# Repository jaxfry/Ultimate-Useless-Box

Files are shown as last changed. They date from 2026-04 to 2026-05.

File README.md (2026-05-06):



[][stars-url]
[][issues-url]
[][license-url]

<!-- PROJECT LOGO -->
<br />
<div align="center">
  <a href="https://github.com/jaxfry/Ultimate-Useless-Box">
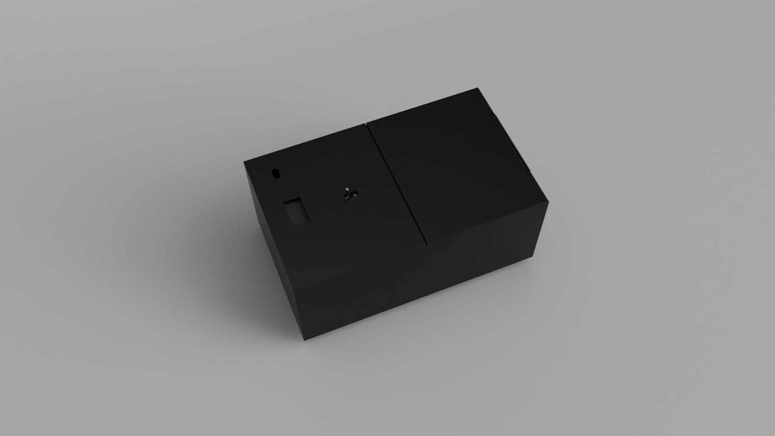
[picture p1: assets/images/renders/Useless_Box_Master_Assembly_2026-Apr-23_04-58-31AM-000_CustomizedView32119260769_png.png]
    
  </a>

<h3 align="center">Ultimate Useless Box</h3>

  <p align="center">
    The Ultimate Useless Box, a box that does nothing, with style.
    <br />
    <br />
    <a href="#gallery--renders">View Renders</a>
    &middot;
    <a href="#custom-pcb">View PCB</a>
  </p>
</div>

<!-- TABLE OF CONTENTS -->
<details>
  <summary>Table of Contents</summary>
  <ol>
    <li>
      <a href="#about-the-project">About The Project</a>
      <ul>
        <li><a href="#built-with">Built With</a></li>
      </ul>
    </li>
    <li>
      <a href="#gallery--renders">Gallery & Renders</a>
    </li>
    <li>
      <a href="#custom-pcb">Custom PCB</a>
    </li>
    <li><a href="#bill-of-materials">Bill of Materials</a></li>
    <li><a href="#license">License</a></li>
  </ol>
</details>

<!-- ABOUT THE PROJECT -->
## About The Project

While most useless boxes just flip a switch, this one has personality. Powered by an **ESP32-S3**, this box uses a Time-of-Flight sensor to detect your hand before you even push the swtich, allowing the box to react by driving away, with the OLED screen, or countless other ways!
This project is heavily inspired by LuuMa EV3.
When I saw that video many years ago, I realized I wanted my own useless box. Then I realized that Lego Mindstorm kits are prohibitively expensive. Many years later and I decided to make my own using standard electronic components with a few unique twists of my own :)

**Key Features:**
* **OLED Display** for animated faces.
* **Fun Built in Power Management:** Mainly for learning and fun but we charge over usb-C!
* **Wheels** for driving away.
* **TOF** sensor for detecting hands.
* **A Retractable Switch**
<p align="right">(<a href="#readme-top">back to top</a>)</p>

### Built With

*   
*   
*   
*   

<p align="right">(<a href="#readme-top">back to top</a>)</p>

### Custom PCB
<div align="center">
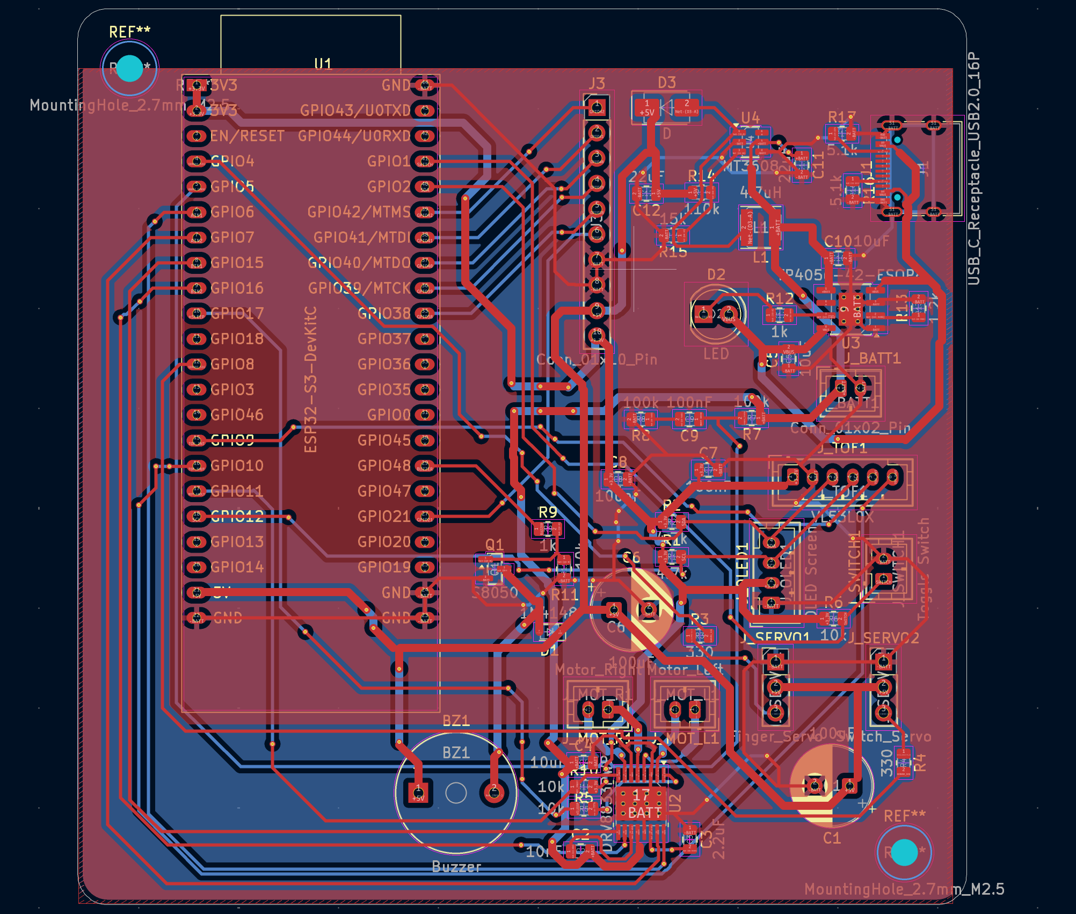
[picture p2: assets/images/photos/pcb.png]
PCB Front
  
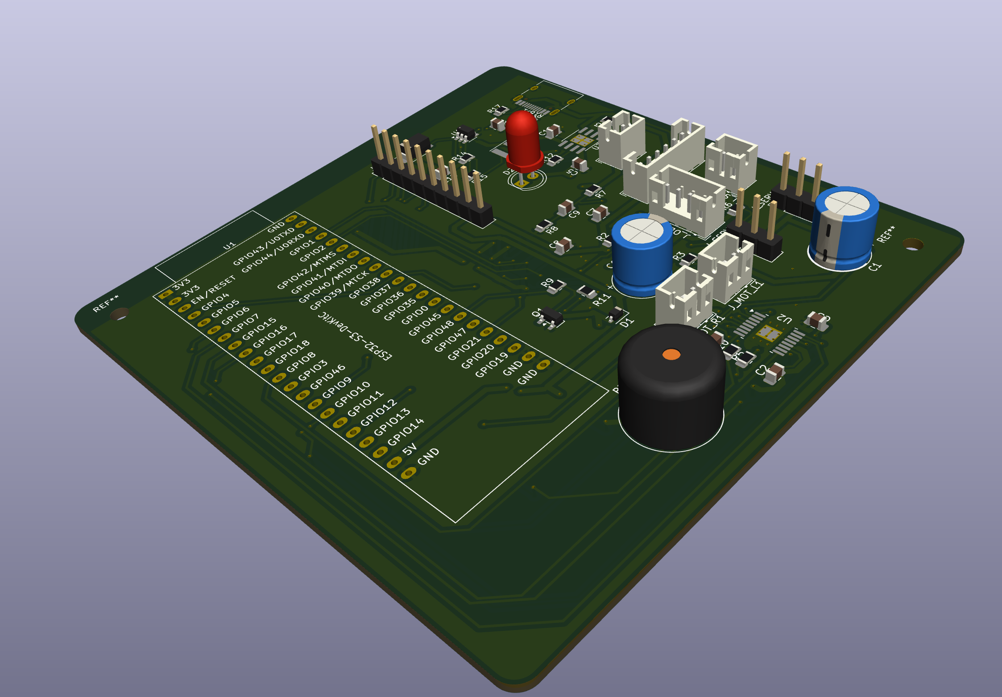
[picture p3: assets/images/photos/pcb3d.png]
PCB 3D View
  
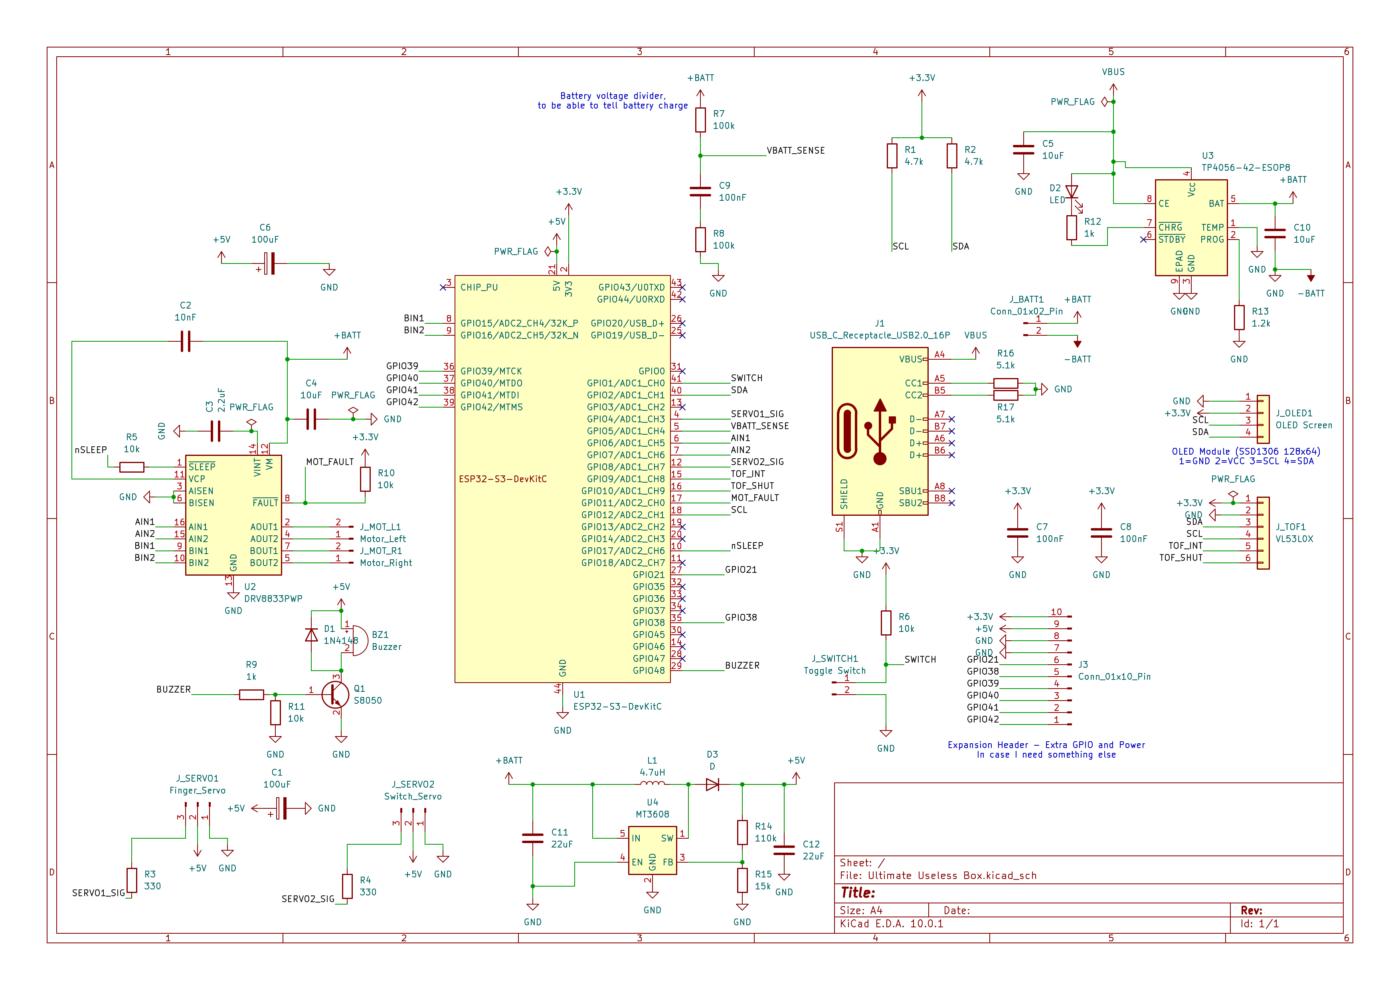
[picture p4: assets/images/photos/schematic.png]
Schematic Diagram
    
</div>

<!-- GALLERY -->
<h2 id="gallery--renders">Gallery & Renders</h2>

<div align="center">
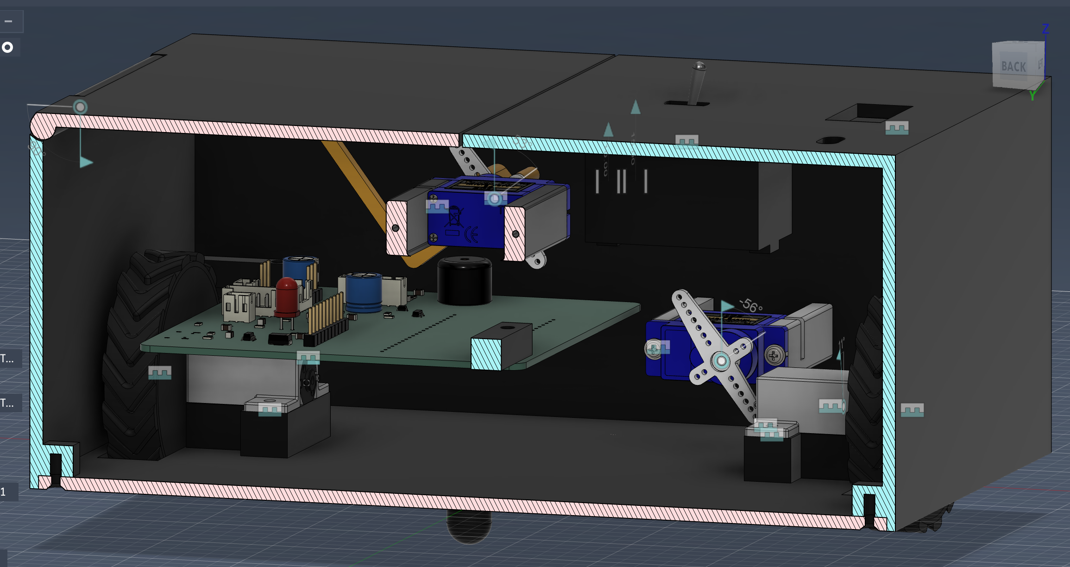
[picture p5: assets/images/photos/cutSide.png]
Cut Side Photo
  
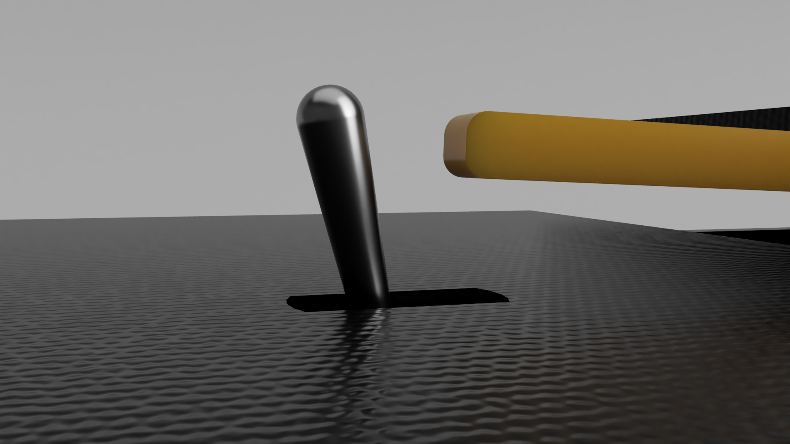
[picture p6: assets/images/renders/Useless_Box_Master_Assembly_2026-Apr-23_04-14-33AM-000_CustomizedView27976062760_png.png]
Render View 1
  
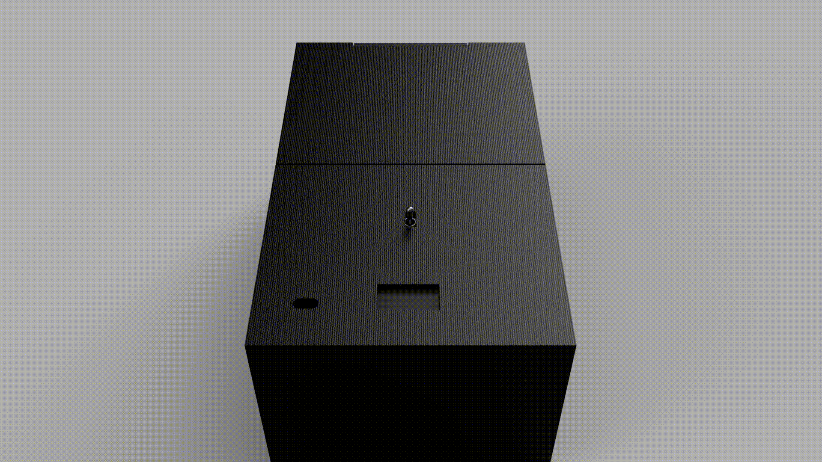
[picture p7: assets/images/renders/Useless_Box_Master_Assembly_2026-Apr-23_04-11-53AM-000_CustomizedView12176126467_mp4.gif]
Animated Render 1
  
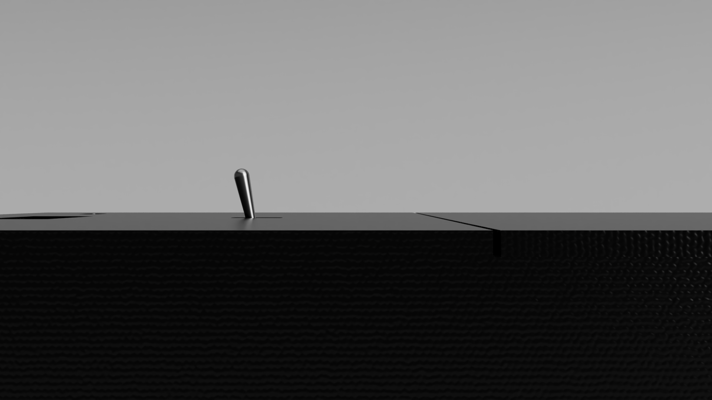
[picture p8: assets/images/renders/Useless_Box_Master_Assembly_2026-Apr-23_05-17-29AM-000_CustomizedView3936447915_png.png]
Render View 3
  
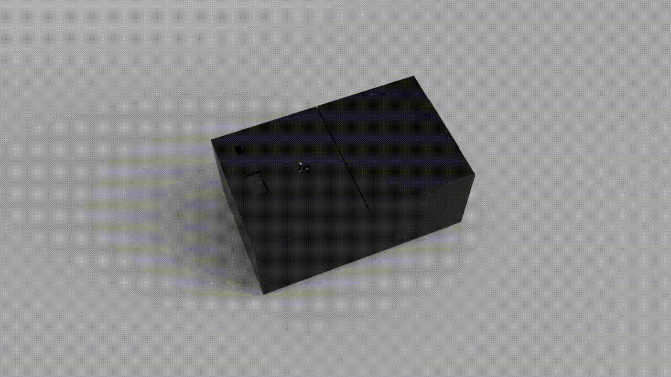
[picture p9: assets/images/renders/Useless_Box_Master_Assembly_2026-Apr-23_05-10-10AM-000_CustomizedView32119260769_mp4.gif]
Animated Render 2
  
</div>

<p align="right">(<a href="#readme-top">back to top</a>)</p>

### Project Goals
- Build a reliable useless box with some personality
- Use accessible parts and open files
- Learn more about PCB design

## How to build
It should be pretty easy, the PCB has labeled connectors for what you need to plug in where. Basically, plug the servos into the headers labeled servos, the motors into the ports labeled motor right and motor left, the TOF sensor into TOF and switch into Switch, and you should be good to go.

<p align="right">(<a href="#readme-top">back to top</a>)</p>

<!-- MARKDOWN LINKS & IMAGES -->
<!-- https://www.markdownguide.org/basic-syntax/#reference-style-links -->
[stars-shield]: https://img.shields.io/github/stars/jaxfry/Ultimate-Useless-Box.svg?style=for-the-badge
[stars-url]: https://github.com/jaxfry/Ultimate-Useless-Box/stargazers
[issues-shield]: https://img.shields.io/github/issues/jaxfry/Ultimate-Useless-Box.svg?style=for-the-badge
[issues-url]: https://github.com/jaxfry/Ultimate-Useless-Box/issues
[license-shield]: https://img.shields.io/github/license/jaxfry/Ultimate-Useless-Box.svg?style=for-the-badge
[license-url]: https://github.com/jaxfry/Ultimate-Useless-Box/blob/main/LICENSE.txt

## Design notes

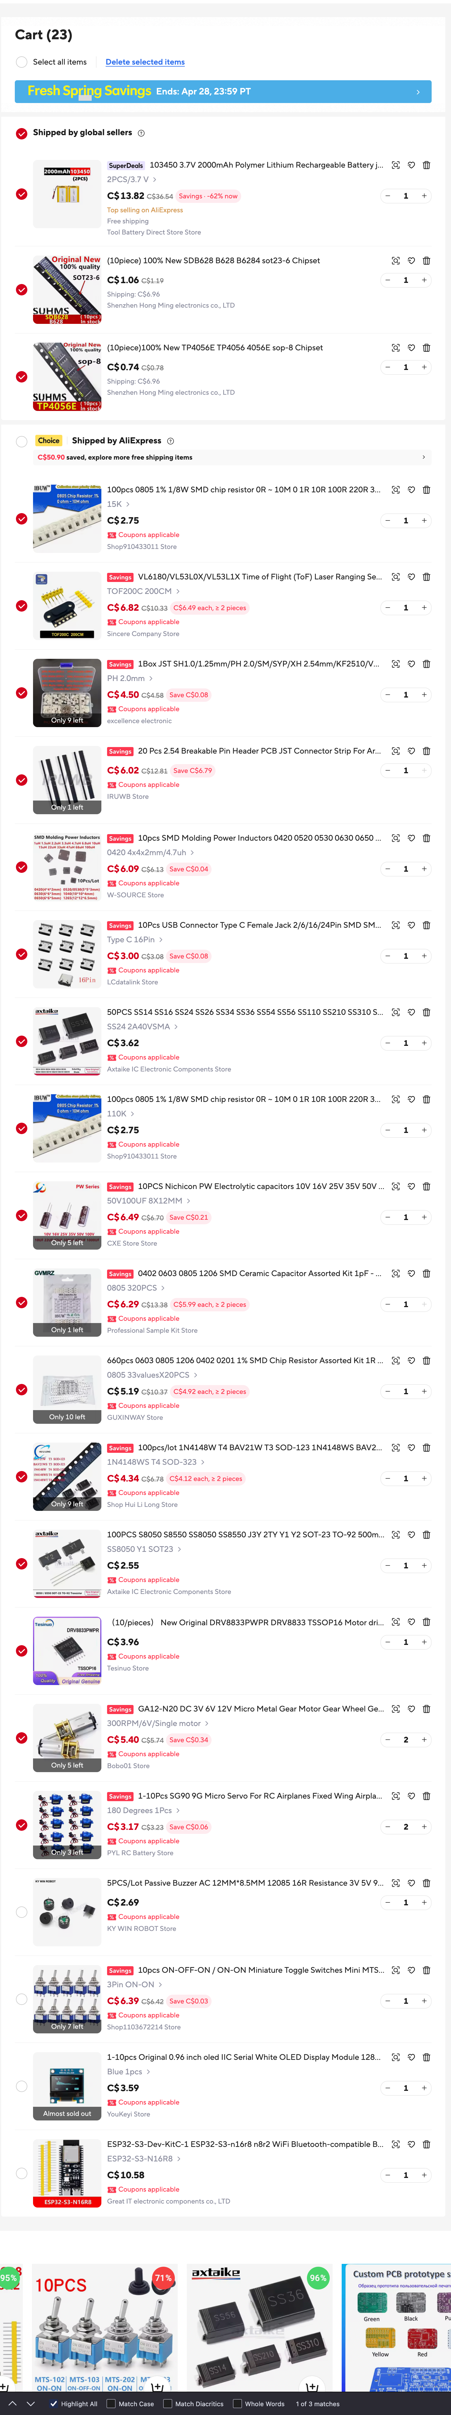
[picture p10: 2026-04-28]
assets/images/photos/cart.png

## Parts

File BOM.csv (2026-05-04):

Name | Purpose | Quantity | Total Cost (USD) | Link | Distributor
PCB | Main control board fabrication | 1 | 3.48 | https://jlcpcb.com/ | JLCPCB
(10piece)100% New TP4056E TP4056 4056E sop-8 Chipset | Charge the battery | 1 | 0.50 | https://www.aliexpress.com/item/32714366180.html | Aliexpress
(10piece) 100% New SDB628 B628 B6284 sot23-6 Chipset | The converter | 1 | 0.74 | https://www.aliexpress.com/item/32868057947.html | Aliexpress
100pcs 0805 1% 1/8W SMD chip resistor 0R ~ 10M 0 1R 10R 100R 220R 330R 470R 1K 4.7K 10K 47K 100K 1M 10M 0 1 10 100 330 470 ohm (15k) | TO resist | 1 | 1.98 | https://www.aliexpress.com/item/1005001437042051.html | Aliexpress
100pcs 0805 1% 1/8W SMD chip resistor 0R ~ 10M 0 1R 10R 100R 220R 330R 470R 1K 4.7K 10K 47K 100K 1M 10M 0 1 10 100 330 470 ohm (110K) | To Provide Resistance | 1 | 1.98 | https://www.aliexpress.com/item/1005001437042051.html | Aliexpress
100PCS SS14 SS24 SS34 SS16 SS26 SS36 SS110 SS210 SS310 SS54 SS56 SS510 1A 40V SMA DO-214AC SMD Schottky Diodes (SS24 SMA) | For the booster | 1 | 2.66 | https://www.aliexpress.com/item/1005005609558264.html | Aliexpress
10Pcs USB Connector Type C Female Jack 2/6/16/24Pin SMD SMT Type-C Socket Charging Port For PCB Soldering DIY Repair Adapter (Color: Type C 16Pin) | Charging | 1 | 2.10 | https://www.aliexpress.com/item/1005007426642375.html | Aliexpress
10pcs SMD Molding Power Inductors 0420 0520 0530 0630 0650 1uH 1.5uH 2.2uH 3.3uH 4.7uH 6.8uH 10uH 15uH 22uH 33uH 47uH Inductor (Volume: 0420 4x4x2mm Value of Resistance: 4.7uh) | Boost Circuit | 1 | 4.29 | https://www.aliexpress.com/item/1005007254030376.html | Aliexpress
20 Pcs 2.54 Breakable Pin Header PCB JST Connector Strip For Arduino DIY Kit 10 Pairs 40 Pin 1x40 Single Row Male And Female | Connecting components & ESP32 | 1 | 4.48 | https://www.aliexpress.com/item/1005010347602299.html | Aliexpress
1Box JST SH1.0/1.25mm/PH 2.0/SM/SYP/XH 2.54mm/KF2510/VH 3.96mm Pitch Terminal Kit Male Female Housing Pin Header JST Connector (PH 2.0mm) | Connecting | 1 | 3.09 | https://www.aliexpress.com/item/1005008783240077.html | Aliexpress
10PCS Nichicon PW Electrolytic capacitors 10V 16V 25V 35V 50V 63V 100V 10UF 22UF 47UF 100UF 220UF 470UF 820UF 1000UF 1200UF NEW (Capacitance: 50V100UF 8X12MM) | Keep motors ready for action! | 1 | 4.79 | https://www.aliexpress.com/item/1005009257286633.html | Aliexpress
0402 0603 0805 1206 SMD Ceramic Capacitor Assorted Kit 1pF - 10uF 100PF 10NF 100NF 0.47UF 1UF Chip Capacitance Set (0805 320PCS) | Keep those components nice and powered | 1 | 4.55 | https://www.aliexpress.com/i/1005010516436707.html?tt=CPS_NORMAL&af=1010595&cv=47843 | Aliexpress
660pcs 0603 0805 1206 0402 0201 1% SMD Chip Resistor Assorted Kit 1R - 1M ohm 33valuesX20pcs Resistance Sample Set (0805 33valuesX20PCS) | Resistors for the board | 1 | 3.59 | https://www.aliexpress.com/item/1005009735103526.html | Aliexpress
100pcs/lot 1N4148W T4 BAV21W T3 SOD-123 1N4148WS BAV21WS SOD-323 1N4148WT SOD-523 1N4148 BAV21 BAV21W SMD Switching Diodes (1N4148WS T4 SOD-323) | Protect that buzzer! | 1 | 3.42 | https://www.aliexpress.com/item/1005007160563285.html | Aliexpress
100PCS S8050 S8550 SS8050 SS8550 J3Y 2TY Y1 Y2 SOT-23 TO-92 500mA 0.5A 1.5A 25V 40V NPN PNP MMBT 8050 8550 SMD DIP Transistor (SS8050 Y1 SOT23) | Component | 1 | 1.81 | https://www.aliexpress.com/item/1005005647370601.html | Aliexpress
（10/pieces） New Original DRV8833PWPR DRV8833 TSSOP16 Motor driver chip In Stock | To control the motors | 1 | 2.85 | https://www.aliexpress.com/item/1005008641599688.html | Aliexpress
103450 3.7V 2000mAh Polymer Lithium Rechargeable Battery jst PH 2.0mm 2pin plug for Camera GPS navigator MP5 Bluetooth Headset | To power the box | 1 | 5.76 | https://www.aliexpress.com/item/1005009590723370.html | Aliexpress
GA12-N20 DC 3V 6V 12V Micro Metal Gear Motor Gear Wheel Gear Motor 30RPM 50RPM 60RPM 100RPM 150RPM 200RPM 300RPM 600RPM 1000RPM | Moving the box | 2 | 8.32 | https://www.aliexpress.com/item/1005005699205905.html | Aliexpress
1-10Pcs SG90 9G Micro Servo For RC Airplanes Fixed Wing Airplane Model Telecontrol Airplane Toy Mini Servo Motor 450 Helicopter | Pushing the servo | 1 | 4.10 | https://www.aliexpress.com/item/1005007173214082.html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 | Aliexpress
5PCS/Lot Passive Buzzer AC 12MM*8.5MM 12085 16R Resistance 3V 5V 9V 12V In Common Use New Wholesale | Make fun sounds | 1 | 1.80 | https://www.aliexpress.com/item/32950836255.html | Aliexpress
10pcs ON-OFF-ON / ON-ON Miniature Toggle Switches Mini MTS-102 103 202 203 Power Button Switch 3pin 6pin | The main switch | 1 | 4.50 | https://www.aliexpress.com/i/1005008778471415.html?af=1010595&cv=47843 | Aliexpress
VL6180/VL53L0X/VL53L1X Time of Flight (ToF) Laser Ranging Sensor Module TOF050C TOF200C TOF400C 50CM/2M/4M IIC For Arduino STM32 | Detecting hands | 2 | 4.93 | https://www.aliexpress.com/item/1005006148761687.html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 | Aliexpress
1-10pcs Original 0.96 inch oled IIC Serial White OLED Display Module 128X64 I2C SSD1306 12864 LCD Screen Board For Arduino | For extra fun >:) It's a screen. | 1 | 3.65 | https://www.aliexpress.com/item/1005006141235306.html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 | Aliexpress
ESP32-S3-Dev-KitC-1 ESP32-S3-n16r8 n8r2 WiFi Bluetooth-compatible BLE 5.0 Mesh Development Board ESP32 Wireless Module | The brains of the project | 1 | 8.89 | https://www.aliexpress.com/item/1005005481618843.html | Aliexpress

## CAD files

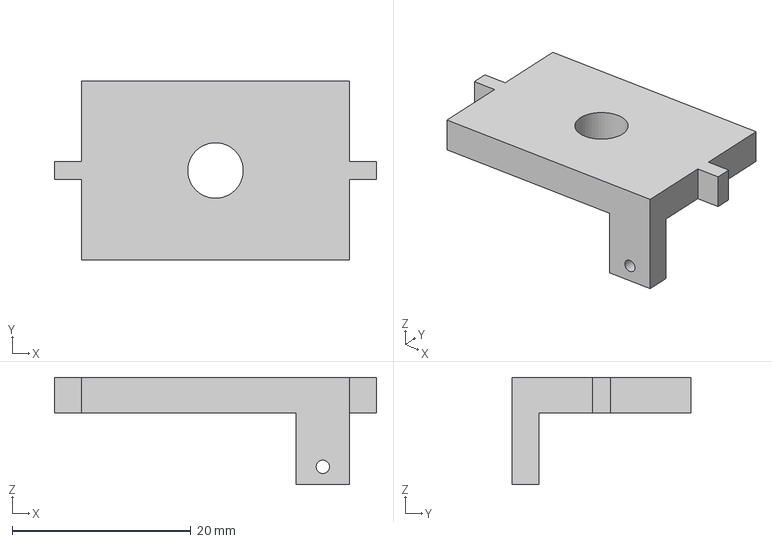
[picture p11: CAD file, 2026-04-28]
cad/3mf/Elevator Platform.3mf
36.0 x 20.0 x 12.0 mm

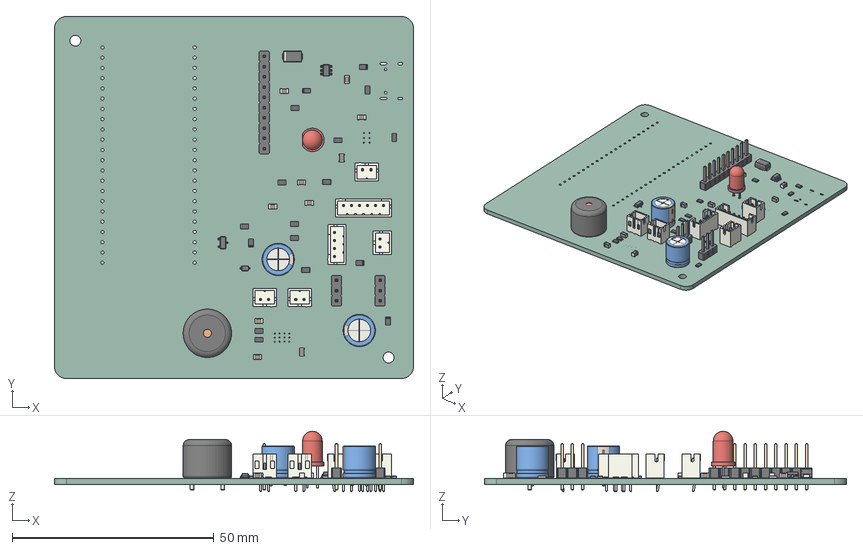
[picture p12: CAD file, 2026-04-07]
pcb/kicad/Ultimate Useless Box.step
89.0 x 89.7 x 15.0 mm
C_0805_2012Metric x 10
R_0805_2012Metric x 17
CP_Radial_D8.0mm_P3.50mm x 2
Buzzer_12x9.5RM7.6
SOT-23-6
JST_PH_B2B-PH-K_1x02_P2.00mm_Vertical x 4
JST_PH_B6B-PH-K_1x06_P2.00mm_Vertical
JST_PH_B4B-PH-K_1x04_P2.00mm_Vertical
PinHeader_1x10_P2.54mm_Vertical
PinHeader_1x03_P2.54mm_Vertical x 2
LED_D5.0mm
D_SOD-323
D_SMA
SOT-23
Ultimate Useless Box_PCB

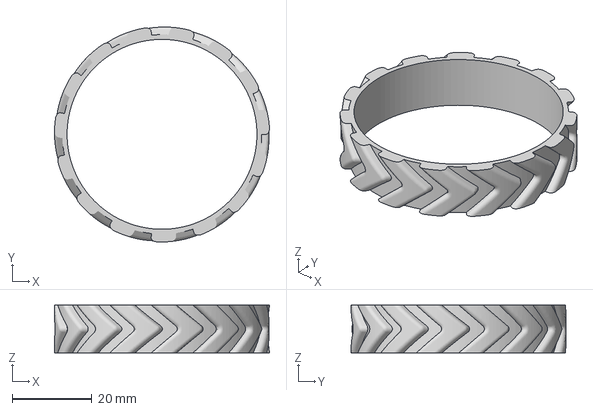
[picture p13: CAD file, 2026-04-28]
cad/3mf/WheelTireTPU.3mf
53.9 x 53.9 x 12.0 mm

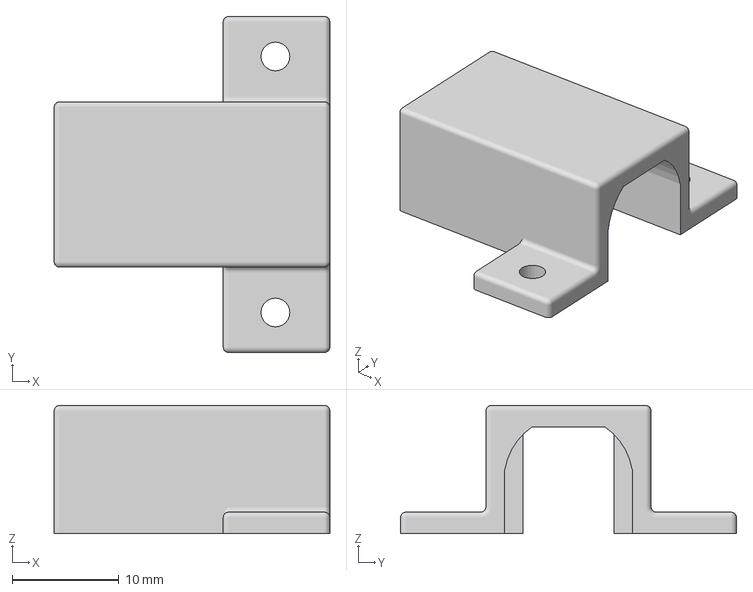
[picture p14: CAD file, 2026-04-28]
cad/3mf/Motor_mount_v31.3mf
25.9 x 31.5 x 12.0 mm

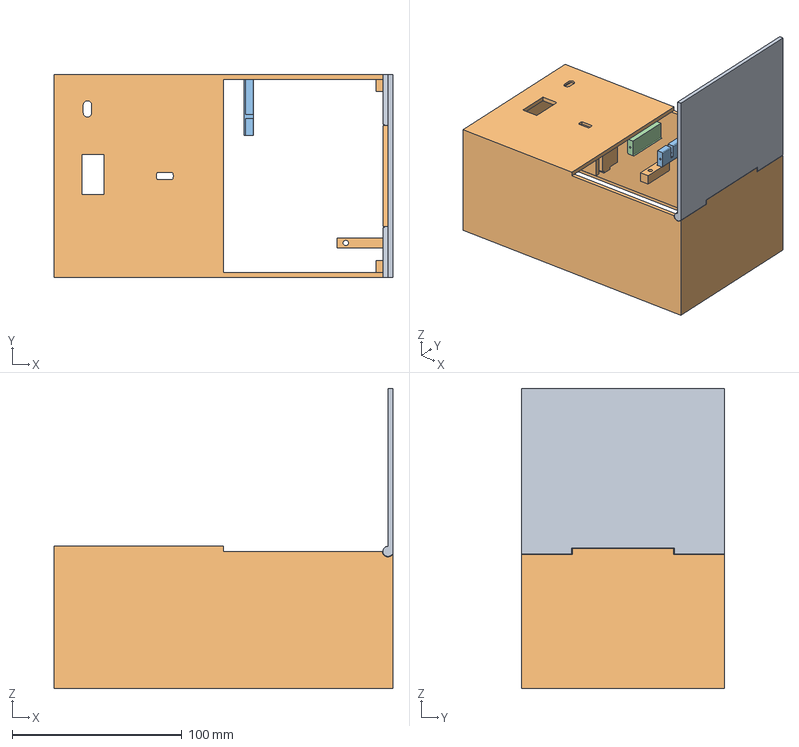
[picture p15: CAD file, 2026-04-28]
cad/3mf/BoxShell.3mf
200.0 x 120.0 x 177.1 mm

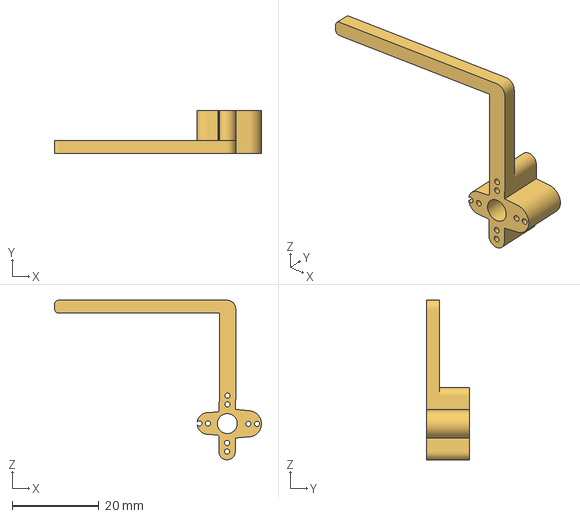
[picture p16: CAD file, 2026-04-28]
cad/3mf/Finger.3mf
47.7 x 10.0 x 36.8 mm

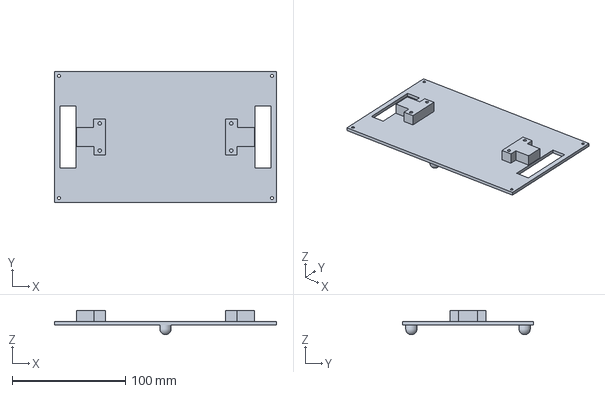
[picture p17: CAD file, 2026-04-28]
cad/3mf/BottomShell_v31.3mf
196.0 x 116.0 x 21.5 mm

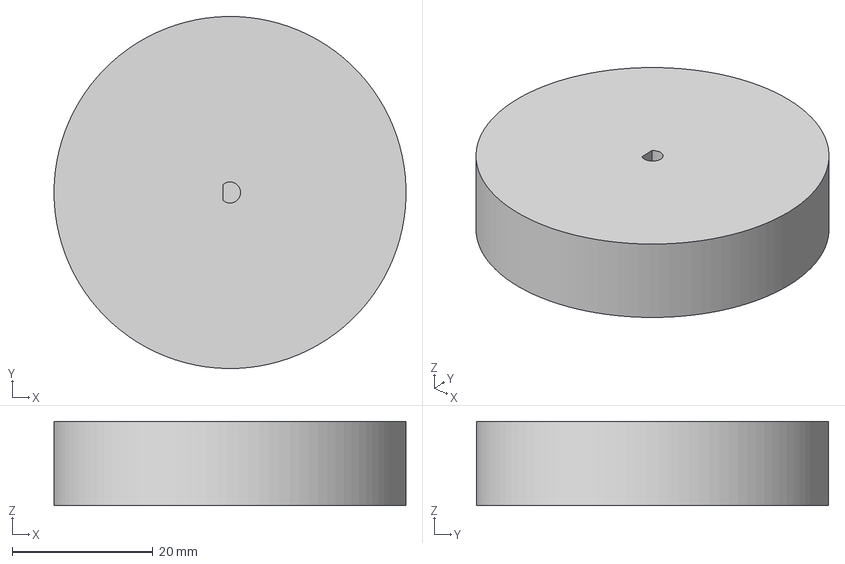
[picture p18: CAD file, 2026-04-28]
cad/3mf/WheelCore.3mf
50.0 x 50.0 x 12.0 mm

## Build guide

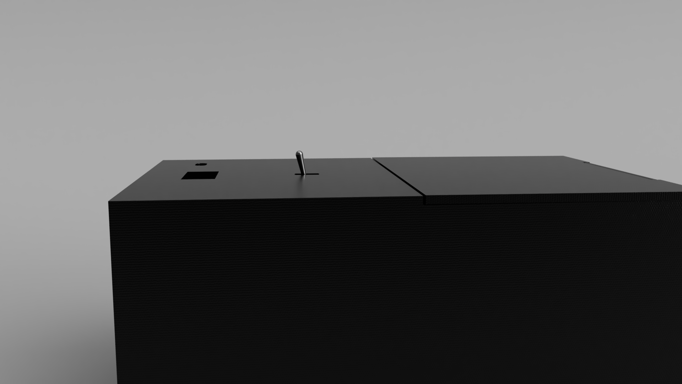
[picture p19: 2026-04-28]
assets/images/renders/Useless_Box_Master_Assembly_2026-Apr-23_04-41-11AM-000_CustomizedView33099754653_png.png

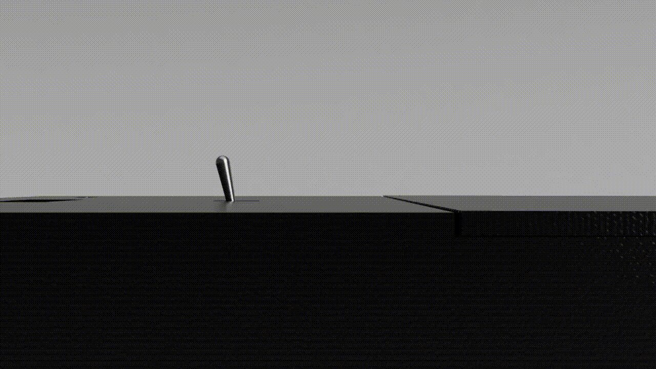
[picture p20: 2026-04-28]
assets/images/renders/Useless_Box_Master_Assembly_2026-Apr-23_05-26-29AM-000_CustomizedView3936447915_mp4.gif

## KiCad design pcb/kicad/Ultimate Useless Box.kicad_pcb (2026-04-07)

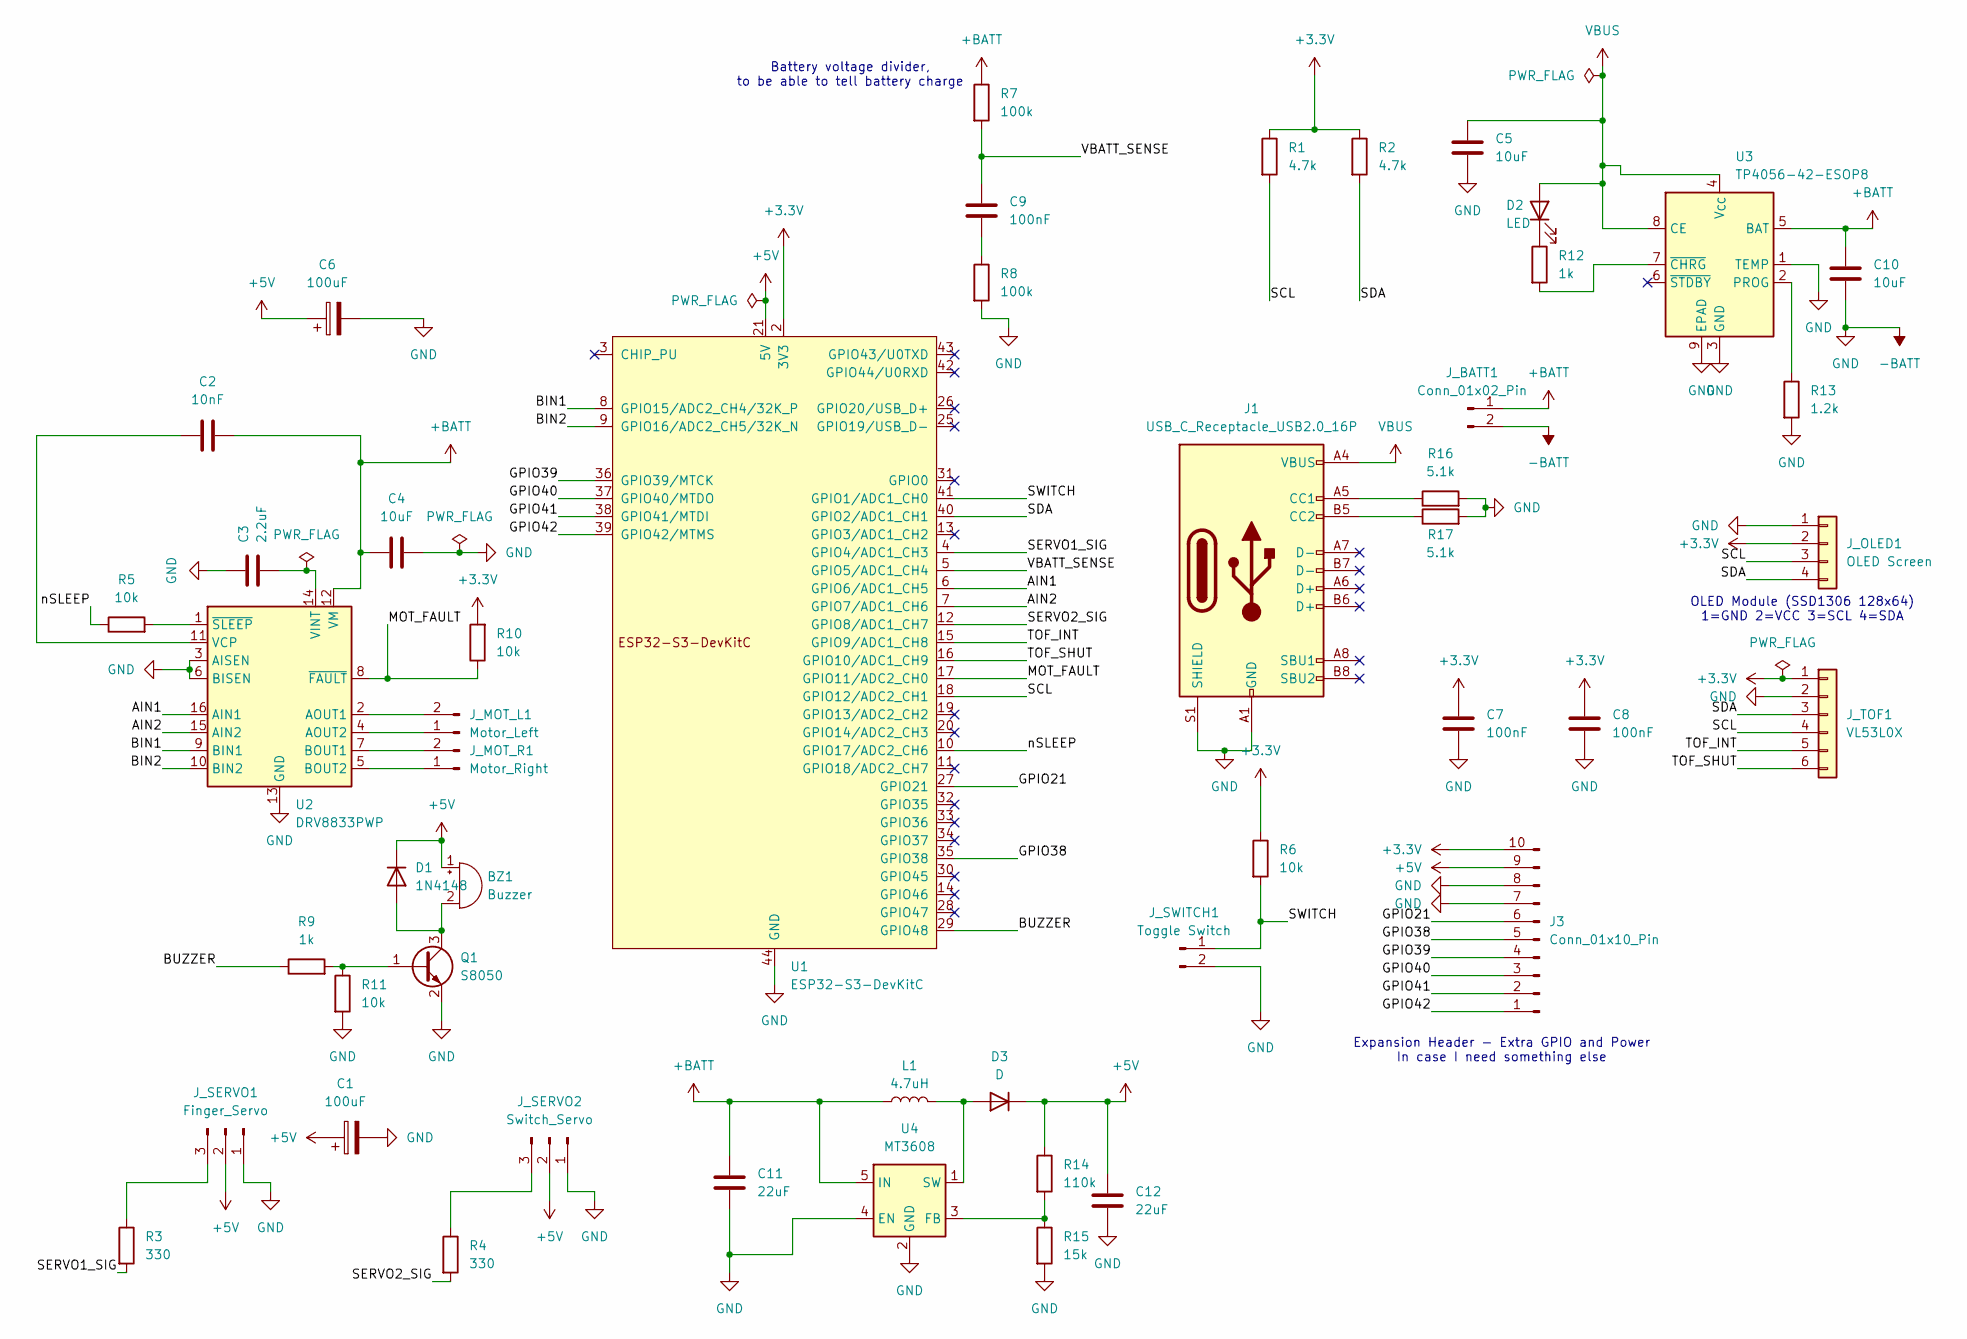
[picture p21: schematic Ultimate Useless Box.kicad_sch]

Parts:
BZ1: Buzzer; Buzzer_12x9.5RM7.6
C1, C6: 100uF; CP_Radial_D8.0mm_P3.50mm
C2: 10nF; C_0805_2012Metric
C3: 2.2uF; C_0805_2012Metric
C4, C5, C10: 10uF; C_0805_2012Metric
C7, C8, C9: 100nF; C_0805_2012Metric
C11, C12: 22uF; C_0805_2012Metric
D1: 1N4148; D_SOD-323
D2: LED; LED_D5.0mm
D3: D; D_SMA
J1: USB_C_Receptacle_USB2.0_16P; USB_C_Receptacle_HRO_TYPE-C-31-M-12
J3: Conn_01x10_Pin; PinHeader_1x10_P2.54mm_Vertical
J_BATT1: Conn_01x02_Pin; JST_PH_B2B-PH-K_1x02_P2.00mm_Vertical
J_MOT_L1: Motor_Left; JST_PH_B2B-PH-K_1x02_P2.00mm_Vertical
J_MOT_R1: Motor_Right; JST_PH_B2B-PH-K_1x02_P2.00mm_Vertical
J_OLED1: OLED Screen; JST_PH_B4B-PH-K_1x04_P2.00mm_Vertical
J_SERVO1: Finger_Servo; PinHeader_1x03_P2.54mm_Vertical
J_SERVO2: Switch_Servo; PinHeader_1x03_P2.54mm_Vertical
J_SWITCH1: Toggle Switch; JST_PH_B2B-PH-K_1x02_P2.00mm_Vertical
J_TOF1: VL53L0X; JST_PH_B6B-PH-K_1x06_P2.00mm_Vertical
L1: 4.7uH; L_Taiyo-Yuden_NR-40xx
Q1: S8050; SOT-23
R1, R2: 4.7k; R_0805_2012Metric
R3, R4: 330; R_0805_2012Metric
R5, R6, R10, R11: 10k; R_0805_2012Metric
R7, R8: 100k; R_0805_2012Metric
R9, R12: 1k; R_0805_2012Metric
R13: 1.2k; R_0805_2012Metric
R14: 110k; R_0805_2012Metric
R15: 15k; R_0805_2012Metric
R16, R17: 5.1k; R_0805_2012Metric
U1: ESP32-S3-DevKitC
U2: DRV8833PWP; HTSSOP-16-1EP_4.4x5mm_P0.65mm_EP3.4x5mm_Mask2.46x2.31mm_The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
U3: TP4056-42-ESOP8; SOIC-8-1EP_3.9x4.9mm_P1.27mm_EP2.41x3.3mm_ThermalVias
U4: MT3608; SOT-23-6

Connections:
+3.3V: C7.1, C8.1, J3.10, J_OLED1.2, J_TOF1.1, R1.1, R2.1, R6.1, R10.2, U1.1 (3V3), U1.2 (3V3)
+5V: BZ1.1 (+), C1.1, C6.1, C12.1, D1.1 (K), D3.1 (K), J3.9, J_SERVO1.2, J_SERVO2.2, R14.1, U1.21 (5V)
+BATT: C2.2, C4.1, C10.1, C11.1, J_BATT1.1, L1.1, R7.1, U2.12 (VM), U3.5 (BAT), U4.5 (IN)
-BATT: C1.2, C3.1, C4.2, C5.1, C6.2, C7.2, C8.2, C10.2, C11.2, C12.2, J1.A1 (GND), J1.A12 (GND), J1.B1 (GND), J1.B12 (GND), J1.S1 (SHIELD), J3.7, J3.8, J_BATT1.2, J_OLED1.1, J_SERVO1.1, J_SERVO2.1, J_SWITCH1.2, J_TOF1.2, Q1.2 (E), R8.2, R11.2, R13.2, R15.2, R16.2, R17.2, U1.22 (GND), U1.23 (GND), U1.24 (GND), U1.44 (GND), U2.3 (AISEN), U2.6 (BISEN), U2.13 (GND), U2.17 (GND), U3.1 (TEMP), U3.3 (GND), U3.9 (EPAD), U4.2 (GND), U4.4 (EN)
/AIN1: U1.6 (GPIO6/ADC1_CH5), U2.16 (AIN1)
/AIN2: U1.7 (GPIO7/ADC1_CH6), U2.15 (AIN2)
/BIN1: U1.8 (GPIO15/ADC2_CH4/32K_P), U2.9 (BIN1)
/BIN2: U1.9 (GPIO16/ADC2_CH5/32K_N), U2.10 (BIN2)
/BUZZER: R9.1, U1.29 (GPIO48)
/GPIO21: J3.6, U1.27 (GPIO21)
/GPIO38: J3.5, U1.35 (GPIO38)
/GPIO39: J3.4, U1.36 (GPIO39/MTCK)
/GPIO40: J3.3, U1.37 (GPIO40/MTDO)
/GPIO41: J3.2, U1.38 (GPIO41/MTDI)
/GPIO42: J3.1, U1.39 (GPIO42/MTMS)
/MOT_FAULT: R10.1, U1.17 (GPIO11/ADC2_CH0), U2.8 (~FAULT)
/SCL: J_OLED1.3, J_TOF1.4, R1.2, U1.18 (GPIO12/ADC2_CH1)
/SDA: J_OLED1.4, J_TOF1.3, R2.2, U1.40 (GPIO2/ADC1_CH1)
/SERVO1_SIG: R3.2, U1.4 (GPIO4/ADC1_CH3)
/SERVO2_SIG: R4.2, U1.12 (GPIO8/ADC1_CH7)
/SWITCH: J_SWITCH1.1, R6.2, U1.41 (GPIO1/ADC1_CH0)
/TOF_INT: J_TOF1.5, U1.15 (GPIO9/ADC1_CH8)
/TOF_SHUT: J_TOF1.6, U1.16 (GPIO10/ADC1_CH9)
/VBATT_SENSE: C9.1, R7.2, U1.5 (GPIO5/ADC1_CH4)
/nSLEEP: R5.1, U1.10 (GPIO17/ADC2_CH6)
unnamed: BZ1.2 (-), D1.2 (A), Q1.3 (C)
unnamed: C9.2, R8.1
unnamed: D2.1 (K), R12.1
unnamed: D3.2 (A), L1.2, U4.1 (SW)
unnamed: J1.A5 (CC1), R16.1
unnamed: J1.B5 (CC2), R17.1
unnamed: J_MOT_L1.1, U2.4 (AOUT2)
unnamed: J_MOT_L1.2, U2.2 (AOUT1)
unnamed: J_MOT_R1.1, U2.5 (BOUT2)
unnamed: J_MOT_R1.2, U2.7 (BOUT1)
unnamed: J_SERVO1.3, R3.1
unnamed: J_SERVO2.3, R4.1
unnamed: Q1.1 (B), R9.2, R11.1
unnamed: C2.1, U2.11 (VCP)
unnamed: C3.2, U2.14 (VINT)
unnamed: R5.2, U2.1 (~SLEEP)
unnamed: R13.1, U3.2 (PROG)
unnamed: R12.2, U3.7 (~CHRG)
unnamed: R14.2, R15.1, U4.3 (FB)
VBUS: C5.2, D2.2 (A), J1.A4 (VBUS), J1.A9 (VBUS), J1.B4 (VBUS), J1.B9 (VBUS), U3.4 (V_{CC}), U3.8 (CE)

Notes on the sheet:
Battery voltage divider, to be able to tell battery charge
Expansion Header - Extra GPIO and Power In case I need something else
OLED Module (SSD1306 128x64) 1=GND 2=VCC 3=SCL 4=SDA

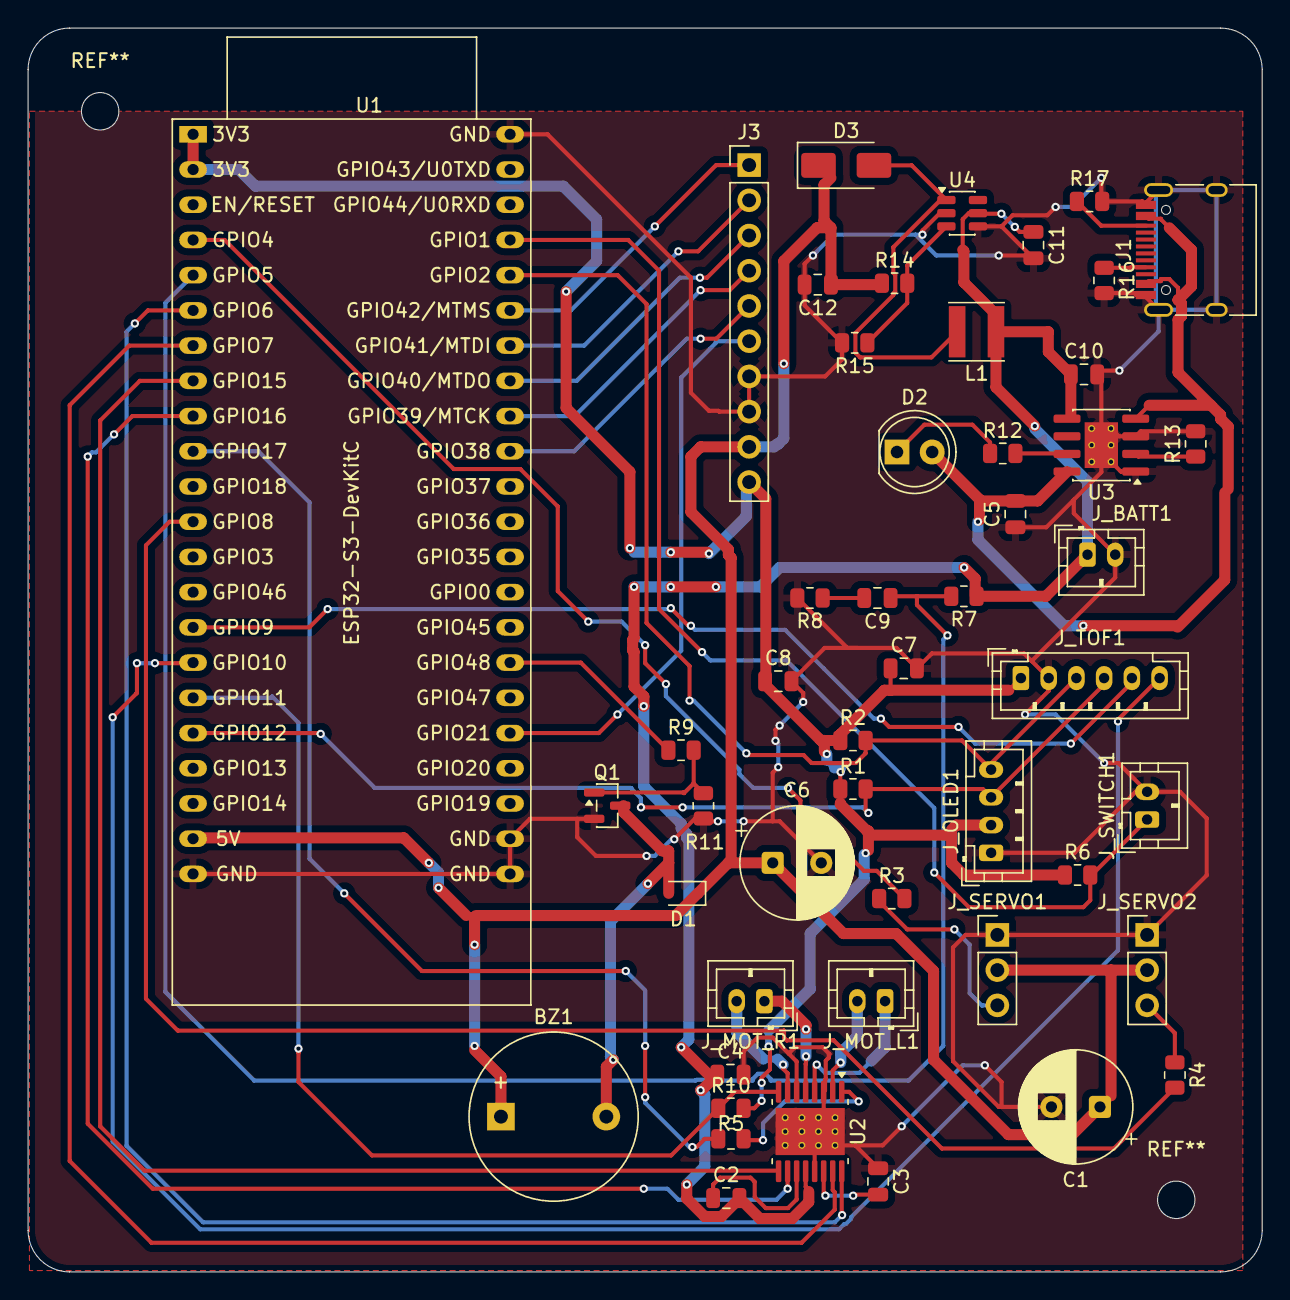
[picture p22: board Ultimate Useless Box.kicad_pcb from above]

Board: 2 copper layers, 89.0 x 89.7 mm, 49 parts (0 on the bottom side), 45 nets.

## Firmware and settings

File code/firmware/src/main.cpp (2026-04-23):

#include <Arduino.h>
#include <Wire.h>
#include <atomic>
#include <Adafruit_GFX.h>
#include <Adafruit_SSD1306.h>
#include <Adafruit_VL53L0X.h>
#include <ESP32Servo.h>

#include "pins.h"
#include "sounds.h"

namespace {
constexpr uint8_t OLED_I2C_ADDRESS = 0x3C;

constexpr TickType_t INPUT_POLL_INTERVAL = pdMS_TO_TICKS(10);
constexpr uint32_t TOF_POLL_PERIOD_MS = 60;
constexpr uint32_t VBATT_POLL_PERIOD_MS = 1000;
constexpr TickType_t BEHAVIOR_LOOP_INTERVAL = pdMS_TO_TICKS(10);
constexpr TickType_t DISPLAY_FRAME_INTERVAL = pdMS_TO_TICKS(33);
constexpr int16_t HAND_DETECTED_MM = 180;
constexpr uint32_t HAND_ACTION_COOLDOWN_MS = 1500;
constexpr uint8_t HAND_REACTION_CHANCE_PERCENT = 35;
constexpr uint8_t SWITCH_HIDE_SERVO_HOME_DEG = 90;
constexpr uint8_t SWITCH_HIDE_SERVO_PULL_IN_DEG = 20;  // Try 160 if your linkage is reversed.
constexpr float VBATT_ADC_DIVIDER_RATIO = 2.0f;  // Adjust if your divider uses a different ratio.
constexpr float VBATT_LOW_THRESHOLD_V = 3.55f;
constexpr float VBATT_CRITICAL_THRESHOLD_V = 3.40f;

Adafruit_SSD1306 display(128, 64, &Wire, -1);
Adafruit_VL53L0X tofSensor;
Servo mainServo;
Servo switchHideServo;

TaskHandle_t sensorTaskHandle = nullptr;
TaskHandle_t behaviorTaskHandle = nullptr;
SemaphoreHandle_t i2cMutex = nullptr;

enum BoxEmotion {
  EMOTION_SLEEPY,
  EMOTION_IDLE,
  EMOTION_ANGRY,
  EMOTION_SURPRISED
};

std::atomic<BoxEmotion> currentEmotion{EMOTION_SLEEPY};
TaskHandle_t displayTaskHandle = nullptr;

// Shared sensor snapshot for future behavior/state tasks.
// Using std::atomic for thread-safe access from multiple cores.
std::atomic<bool> gMainSwitchActive{false};
std::atomic<int16_t> gHandDistanceMm{-1};
std::atomic<bool> gTofSensorPresent{false};
std::atomic<float> gBatteryVoltageV{-1.0f};
std::atomic<bool> gBatteryLow{false};
std::atomic<bool> gBatteryCritical{false};
std::atomic<uint32_t> gEmotionHoldUntilMs{0};
std::atomic<bool> gHasCompletedAnyAction{false};
}  // namespace

void SensorTask(void* pvParameters) {
  (void)pvParameters;

  uint32_t lastTofReadMs = 0;
  uint32_t lastBatteryReadMs = 0;

  for (;;) {
    gMainSwitchActive.store(digitalRead(PIN_MAIN_SWITCH) == LOW);

    uint32_t nowMs = millis();
    if (!gTofSensorPresent.load()) {
      gHandDistanceMm.store(-1);
    } else if (nowMs - lastTofReadMs >= TOF_POLL_PERIOD_MS) {
      VL53L0X_RangingMeasurementData_t measure;
      // Lock I2C mutex to prevent contention with DisplayTask
      if (xSemaphoreTake(i2cMutex, portMAX_DELAY)) {
        tofSensor.rangingTest(&measure, false);
        xSemaphoreGive(i2cMutex);
      }
      gHandDistanceMm.store((measure.RangeStatus != 4) ? measure.RangeMilliMeter : -1);
      lastTofReadMs = nowMs;
    }

    if (nowMs - lastBatteryReadMs >= VBATT_POLL_PERIOD_MS) {
      uint32_t batteryMv = analogReadMilliVolts(PIN_VBATT_SENSE);
      float batteryV = (batteryMv / 1000.0f) * VBATT_ADC_DIVIDER_RATIO;
      gBatteryVoltageV.store(batteryV);
      gBatteryLow.store(batteryV > 0.0f && batteryV <= VBATT_LOW_THRESHOLD_V);
      gBatteryCritical.store(batteryV > 0.0f && batteryV <= VBATT_CRITICAL_THRESHOLD_V);
      lastBatteryReadMs = nowMs;
    }

    vTaskDelay(INPUT_POLL_INTERVAL);
  }
}

// Actions

bool emotionHoldActive() {
  return static_cast<int32_t>(gEmotionHoldUntilMs.load() - millis()) > 0;
}

void holdEmotion(BoxEmotion emotion, uint32_t durationMs) {
  currentEmotion.store(emotion);
  gEmotionHoldUntilMs.store(millis() + durationMs);
}

void actionStandard() {
  // Standard push and return

  holdEmotion(EMOTION_ANGRY, 900);
  soundChirp();

  // Flick switch
  mainServo.write(20);
  vTaskDelay(pdMS_TO_TICKS(320));

  // Home
  mainServo.write(90);
  soundHappy();
  vTaskDelay(pdMS_TO_TICKS(180));
}

void actionHesitant() {
  // Comes out a little bit, goes back, then flicks it.

  holdEmotion(EMOTION_SURPRISED, 1200);
  soundSurprise();
  mainServo.write(65);
  vTaskDelay(pdMS_TO_TICKS(380));

  mainServo.write(90);
  vTaskDelay(pdMS_TO_TICKS(650));

  holdEmotion(EMOTION_ANGRY, 1000);
  soundSass();
  mainServo.write(20);
  vTaskDelay(pdMS_TO_TICKS(320));

  mainServo.write(90);
  soundHappy();
  vTaskDelay(pdMS_TO_TICKS(180));
}

void motorsStop() {
  analogWrite(PIN_MOT_AIN1, 0);
  analogWrite(PIN_MOT_AIN2, 0);
  analogWrite(PIN_MOT_BIN1, 0);
  analogWrite(PIN_MOT_BIN2, 0);
}

void motorsDrive() {
  analogWrite(PIN_MOT_AIN1, 200);
  analogWrite(PIN_MOT_AIN2, 0);
  analogWrite(PIN_MOT_BIN1, 200);
  analogWrite(PIN_MOT_BIN2, 0);
}

void actionDriveAway() {
  holdEmotion(EMOTION_ANGRY, 1000);
  soundGrump();
  motorsDrive();
  vTaskDelay(pdMS_TO_TICKS(400));
  motorsStop();
  vTaskDelay(pdMS_TO_TICKS(200));
}

void actionHideSwitchInside() {
  holdEmotion(EMOTION_SURPRISED, 1100);
  soundWhistle();

  switchHideServo.write(SWITCH_HIDE_SERVO_PULL_IN_DEG);
  vTaskDelay(pdMS_TO_TICKS(550));

  switchHideServo.write(SWITCH_HIDE_SERVO_HOME_DEG);
  soundHappy();
  vTaskDelay(pdMS_TO_TICKS(220));
}

void runRandomAction(bool allowDriveAway) {
  if (allowDriveAway) {
    // Weighted chance: 10% drive away, 45% standard, 45% hesitant.
    int slot = random(0, 10);
    if (slot == 0) {
      actionDriveAway();
    } else if (slot <= 4) {
      actionStandard();
    } else {
      actionHesitant();
    }
  } else {
    // First action after boot: never drive away.
    if (random(0, 2) == 0) {
      actionStandard();
    } else {
      actionHesitant();
    }
  }

  gHasCompletedAnyAction.store(true);
}

void runRandomTofAction() {
  // TOF-specific pool: drive away or pull the switch mechanism inside the box.
  if (!gBatteryLow.load() && random(0, 2) == 0) {
    actionDriveAway();
  } else {
    actionHideSwitchInside();
  }

  gHasCompletedAnyAction.store(true);
}

void BehaviorTask(void* pvParameters) {
  (void)pvParameters;

  bool lastSwitchState = false;
  bool lastHandNear = false;
  uint32_t nextHandActionAllowedMs = 0;

  for (;;) {
    bool currentSwitchState = gMainSwitchActive.load();

    bool handNear = (gHandDistanceMm.load() > 0 && gHandDistanceMm.load() < HAND_DETECTED_MM);
    uint32_t nowMs = millis();
    bool batteryCritical = gBatteryCritical.load();

    if (currentSwitchState == true && lastSwitchState == false) {
      Serial.println(batteryCritical ? "Switch flicked, battery is critical" :
                                       "OMG someone flicked the switch!");
      runRandomAction(gHasCompletedAnyAction.load() && !batteryCritical);
    }

    // Hand-detected trigger: rising edge + cooldown + chance.
    else if (handNear == true && lastHandNear == false &&
             nowMs >= nextHandActionAllowedMs) {
      nextHandActionAllowedMs = nowMs + HAND_ACTION_COOLDOWN_MS;

      if (batteryCritical) {
        Serial.println("Hand detected: skipping action because battery is critical");
      } else if (random(0, 100) < HAND_REACTION_CHANCE_PERCENT) {
        if (gHasCompletedAnyAction.load()) {
          Serial.println("Hand detected: TOF action triggered");
          runRandomTofAction();
        } else {
          Serial.println("Hand detected: TOF actions locked until first action");
        }
      } else {
        Serial.println("Hand detected: ignoring this time");
      }
    }

    lastSwitchState = currentSwitchState;
    lastHandNear = handNear;

    if (!emotionHoldActive()) {
      if (handNear) {
        currentEmotion.store(EMOTION_IDLE);
      } else {
        currentEmotion.store(EMOTION_SLEEPY);
      }
    }

    vTaskDelay(BEHAVIOR_LOOP_INTERVAL);
  }
}

void drawSleepyFace(uint32_t nowMs) {
  const int leftX = 40;
  const int rightX = 88;
  const int eyeY = 30;

  display.drawLine(leftX - 11, eyeY, leftX + 11, eyeY, SSD1306_WHITE);
  display.drawLine(leftX - 11, eyeY + 1, leftX + 11, eyeY + 1, SSD1306_WHITE);
  display.drawLine(rightX - 11, eyeY, rightX + 11, eyeY, SSD1306_WHITE);
  display.drawLine(rightX - 11, eyeY + 1, rightX + 11, eyeY + 1, SSD1306_WHITE);

  uint8_t zPhase = (nowMs / 500) % 6;
  if (zPhase < 5) {
    display.setTextSize(1);
    display.setCursor(8 + (zPhase * 8), 10 - (zPhase / 2));
    display.print("z");
  }
}

void drawIdleFace(uint32_t nowMs) {
  const int leftX = 40;
  const int rightX = 88;
  const int eyeY = 30;
  const int eyeW = 22;

  int eyeHalfH = 8;
  uint32_t cycle = nowMs % 3200;
  if (cycle >= 2800 && cycle < 2910) {
    eyeHalfH = map(cycle, 2800, 2910, 8, 1);
  } else if (cycle >= 2910 && cycle < 3020) {
    eyeHalfH = map(cycle, 2910, 3020, 1, 8);
  }

  display.fillRoundRect(leftX - (eyeW / 2), eyeY - eyeHalfH, eyeW, eyeHalfH * 2, 4,
                        SSD1306_WHITE);
  display.fillRoundRect(rightX - (eyeW / 2), eyeY - eyeHalfH, eyeW, eyeHalfH * 2, 4,
                        SSD1306_WHITE);

  if (eyeHalfH > 3) {
    int lookOffset = (static_cast<int>((nowMs / 250) % 5) - 2) * 2;
    display.fillCircle(leftX + lookOffset, eyeY, 2, SSD1306_BLACK);
    display.fillCircle(rightX + lookOffset, eyeY, 2, SSD1306_BLACK);
  }
}

void drawAngryFace() {
  const int leftX = 40;
  const int rightX = 88;
  const int eyeY = 31;

  display.fillRoundRect(leftX - 12, eyeY - 7, 24, 14, 4, SSD1306_WHITE);
  display.fillRoundRect(rightX - 12, eyeY - 7, 24, 14, 4, SSD1306_WHITE);

  // Carve the top edge to create a stronger, cleaner angry slant.
  display.fillTriangle(leftX - 12, eyeY - 7, leftX + 12, eyeY - 7, leftX + 12, eyeY - 1,
                       SSD1306_BLACK);
  display.fillTriangle(rightX - 12, eyeY - 7, rightX + 12, eyeY - 7, rightX - 12,
                       eyeY - 1, SSD1306_BLACK);

  display.drawLine(leftX - 14, eyeY - 13, leftX + 12, eyeY - 7, SSD1306_WHITE);
  display.drawLine(leftX - 14, eyeY - 12, leftX + 12, eyeY - 6, SSD1306_WHITE);
  display.drawLine(rightX + 14, eyeY - 13, rightX - 12, eyeY - 7, SSD1306_WHITE);
  display.drawLine(rightX + 14, eyeY - 12, rightX - 12, eyeY - 6, SSD1306_WHITE);
}

void drawSurprisedFace(uint32_t nowMs) {
  const int leftX = 40;
  const int rightX = 88;
  const int eyeY = 29;

  int radius = 8 + ((nowMs / 240) % 2);
  display.drawCircle(leftX, eyeY, radius, SSD1306_WHITE);
  display.drawCircle(rightX, eyeY, radius, SSD1306_WHITE);
  display.fillCircle(leftX, eyeY, 2, SSD1306_WHITE);
  display.fillCircle(rightX, eyeY, 2, SSD1306_WHITE);

  int mouthR = 5 + ((nowMs / 180) % 2);
  display.drawCircle(64, 49, mouthR, SSD1306_WHITE);
}

void DisplayTask(void* pvParamters) {
  (void)pvParamters;

  for (;;) {
    uint32_t nowMs = millis();
    display.clearDisplay();

    switch (currentEmotion.load()) {
      case EMOTION_SLEEPY:
        drawSleepyFace(nowMs);
        break;
      case EMOTION_IDLE:
        drawIdleFace(nowMs);
        break;
      case EMOTION_ANGRY:
        drawAngryFace();
        break;
      case EMOTION_SURPRISED:
        drawSurprisedFace(nowMs);
        break;
    }

    // Lock I2C mutex before sending data to OLED
    if (xSemaphoreTake(i2cMutex, portMAX_DELAY)) {
      display.display();
      xSemaphoreGive(i2cMutex);
    }
    vTaskDelay(DISPLAY_FRAME_INTERVAL);
  }
}

void setup() {
  Serial.begin(115200);
  randomSeed(micros());

  pinMode(PIN_MAIN_SWITCH, INPUT_PULLUP);
  pinMode(PIN_VBATT_SENSE, INPUT);
  pinMode(PIN_BUZZER, OUTPUT);
  analogSetPinAttenuation(PIN_VBATT_SENSE, ADC_11db);

  pinMode(PIN_MOT_NSLEEP, OUTPUT);
  digitalWrite(PIN_MOT_NSLEEP, HIGH);

  analogWrite(PIN_MOT_AIN1, 0);
  analogWrite(PIN_MOT_AIN2, 0);
  analogWrite(PIN_MOT_BIN1, 0);
  analogWrite(PIN_MOT_BIN2, 0);

  ESP32PWM::allocateTimer(0);
  ESP32PWM::allocateTimer(1);
  ESP32PWM::allocateTimer(2);
  ESP32PWM::allocateTimer(3);

  mainServo.setPeriodHertz(50);
  mainServo.attach(PIN_SERVO_1, 500, 2400);
  mainServo.write(90);

  switchHideServo.setPeriodHertz(50);
  switchHideServo.attach(PIN_SERVO_2, 500, 2400);
  switchHideServo.write(SWITCH_HIDE_SERVO_HOME_DEG);

  delay(250);

  Wire.begin(PIN_I2C_SDA, PIN_I2C_SCL);

  pinMode(PIN_TOF_SHUT, OUTPUT);
  digitalWrite(PIN_TOF_SHUT, HIGH);
  delay(10);

  if (!tofSensor.begin()) {
    Serial.println(F("VL53L0X init failed"));
    gTofSensorPresent.store(false);
  } else {
    gTofSensorPresent.store(true);
    // Note: Adafruit_VL53L0X doesn't expose setTimeout(), but I2C mutex protects against bus hangs
  }

  bool displayPresent = false;
  if (!display.begin(SSD1306_SWITCHCAPVCC, OLED_I2C_ADDRESS)) {
    Serial.println(F("SSD1306 init failed"));
  } else {
    displayPresent = true;
    display.clearDisplay();
    display.setTextSize(1);
    display.setTextColor(SSD1306_WHITE);
    display.setCursor(0, 0);
    display.println(F("Useless Box Booting..."));
    display.display();
    soundHappy();
  }

  Serial.println(F("Battery monitor enabled on VBATT sense"));

  // Create I2C mutex for thread-safe Wire access
  i2cMutex = xSemaphoreCreateMutex();

  xTaskCreatePinnedToCore(
      SensorTask, "Sensors", 4096, nullptr, 2, &sensorTaskHandle, 0);
  xTaskCreatePinnedToCore(
    BehaviorTask, "Behavior", 4096, nullptr, 2, &behaviorTaskHandle, 1);
  if (displayPresent) {
    xTaskCreatePinnedToCore(
      DisplayTask, "Display", 4096, nullptr, 2, &displayTaskHandle, 1);
  }
}

void loop() {
  vTaskDelete(nullptr);
}

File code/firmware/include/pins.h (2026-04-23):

#pragma once

#include <Arduino.h>

// Inputs
constexpr uint8_t PIN_MAIN_SWITCH = 1;
constexpr uint8_t PIN_VBATT_SENSE = 5;

// I2C bus shared by OLED and ToF.
constexpr uint8_t PIN_I2C_SDA = 2;
constexpr uint8_t PIN_I2C_SCL = 12;

// ToF control lines.
constexpr uint8_t PIN_TOF_SHUT = 10;

// Servo outputs.
constexpr uint8_t PIN_SERVO_1 = 4;
constexpr uint8_t PIN_SERVO_2 = 8;

// DRV8833 control.
constexpr uint8_t PIN_MOT_NSLEEP = 17;

constexpr uint8_t PIN_MOT_AIN1 = 6;
constexpr uint8_t PIN_MOT_AIN2 = 7;

constexpr uint8_t PIN_MOT_BIN1 = 15;
constexpr uint8_t PIN_MOT_BIN2 = 16;

// Audio output.
constexpr uint8_t PIN_BUZZER = 48;

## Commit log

2026-03-06 setup structure
    [master-bom.csv]
2026-03-11 Refactor code structure for improved readability and maintainability
    [Ultimate Useless Box.kicad_pcb, Ultimate Useless Box.kicad_sch, master-bom.csv]
2026-03-12 add GPIO headers, wire sensor
    [master-bom.csv]
2026-03-13 Finish schematic
    [Ultimate Useless Box.kicad_sch, master-bom.csv]
2026-03-22 Finish Kicad
    [Ultimate Useless Box.kicad_pcb, Ultimate Useless Box.kicad_sch]
2026-04-07 Made changes
    [Ultimate Useless Box-B_Cu.gbl, Ultimate Useless Box-B_Mask.gbs, Ultimate Useless Box-B_Paste.gbp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]
2026-04-23 Update CAD and all of the code
    [BOM.csv, master-bom.csv]
2026-04-28 add readme and step files
    [BOM.csv, BottomShell_v31.3mf, BoxShell.3mf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]
2026-05-04 Update BOM & readme
    [BOM.csv]
2026-05-04 remove copy of BOM from readme
2026-05-06 update with schematic
